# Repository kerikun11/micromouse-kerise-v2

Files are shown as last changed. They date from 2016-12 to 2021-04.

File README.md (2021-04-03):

# MicroMouse KERISE v2

クラッシクサイズおよびハーフサイズ兼用マイクロマウス

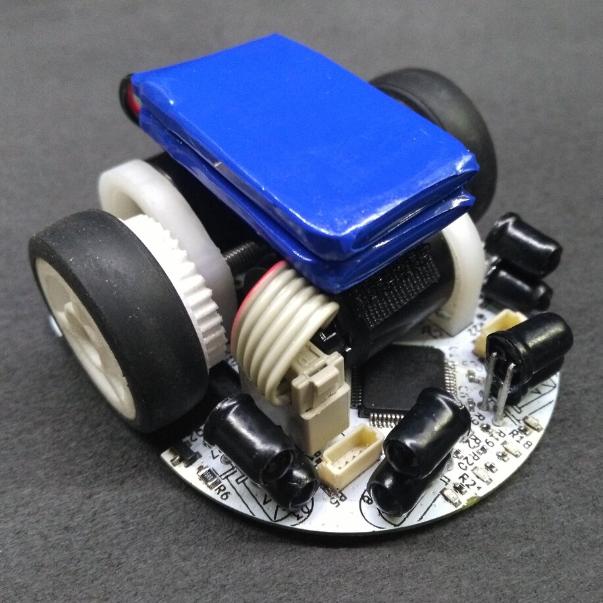
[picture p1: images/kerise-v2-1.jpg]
KERISE v2


## 戦績

なし

## スペック

| 部品 | 型番 | 備考 |
| :--- | :--- | :--- |
| モーター | 1717T006SR | 17mm x 17mm |
| エンコーダ | IEH2-1024 | 1024パルス モーター直結 |
| マイコン | STM32F405RG | 168MHz |
| 赤外線LED | VSLY5850 | 波長850mm 直径5mm |
| フォトダイオード | SFH213FA | 波長900nm 直径5mm |
| モータードライバ | DRV8835 | 最大電流3A |
| 6軸センサ | MPU6500 | 3軸ジャイロ+3軸加速度 |
| バッテリー | LG325-0120-1S-M | 3.7V 25C 120mAh 1S |

## 回路設計

- KiCad

## 開発環境

- mbed RTOS

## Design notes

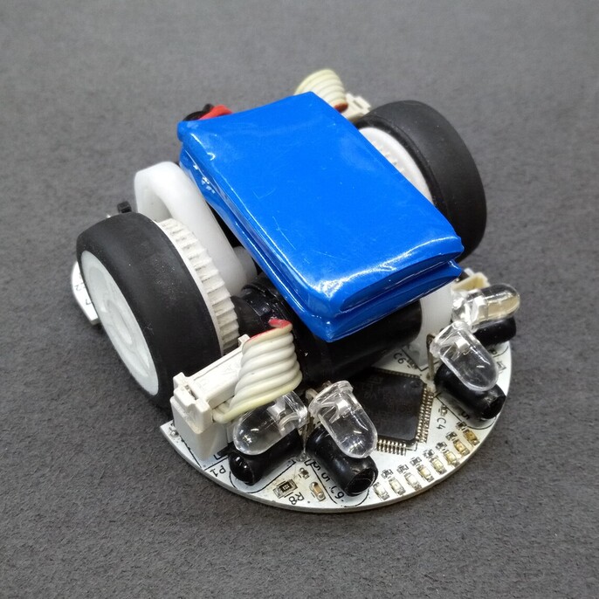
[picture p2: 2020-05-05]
images/kerise-v2-2.jpg

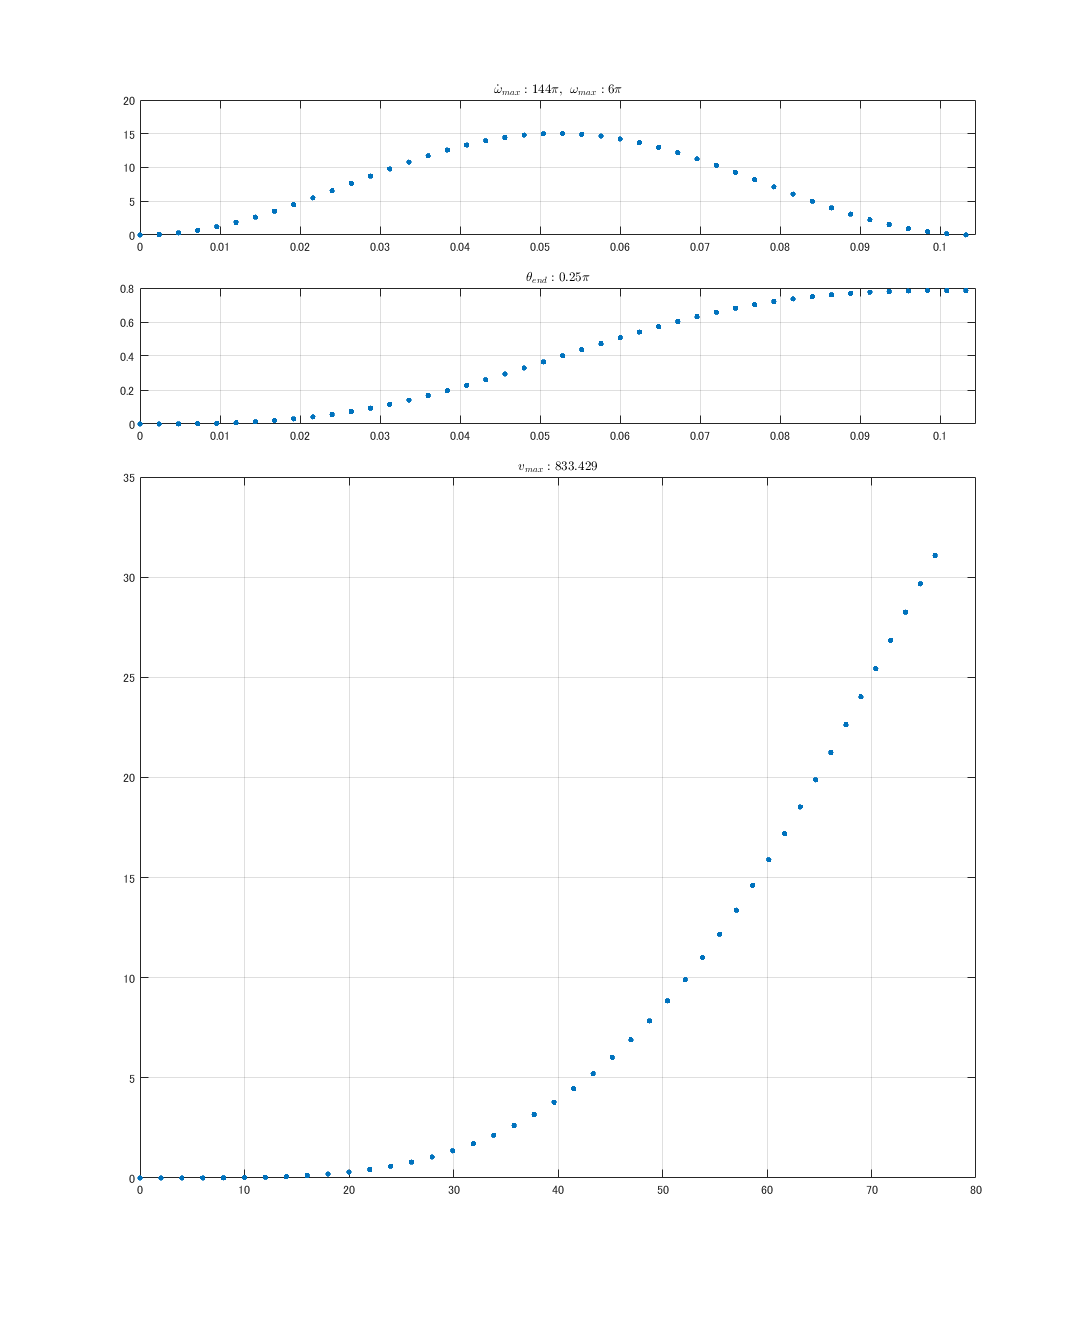
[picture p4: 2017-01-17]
matlab/half45.png

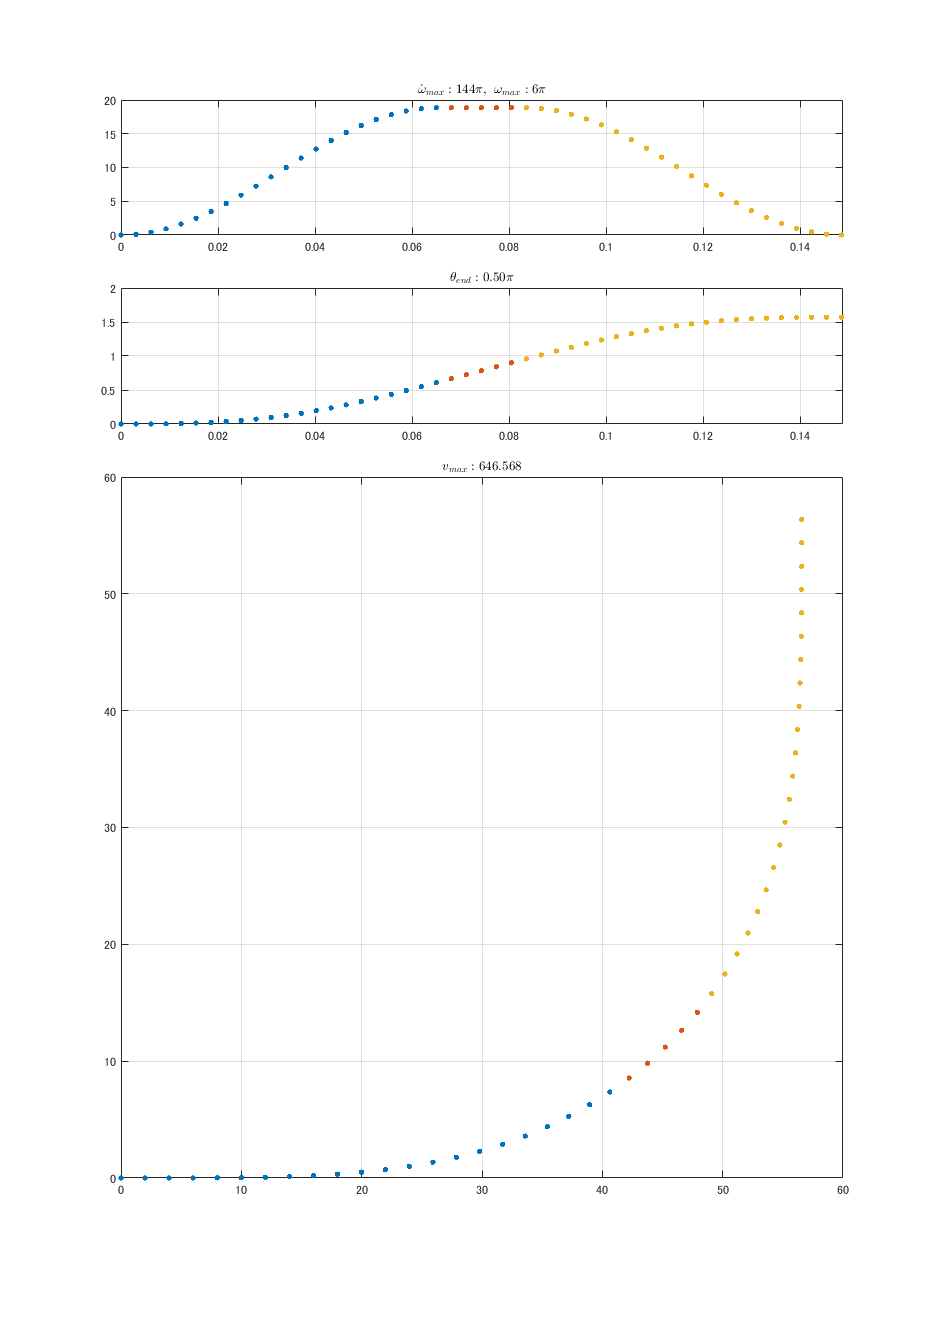
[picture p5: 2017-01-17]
matlab/half4545.png

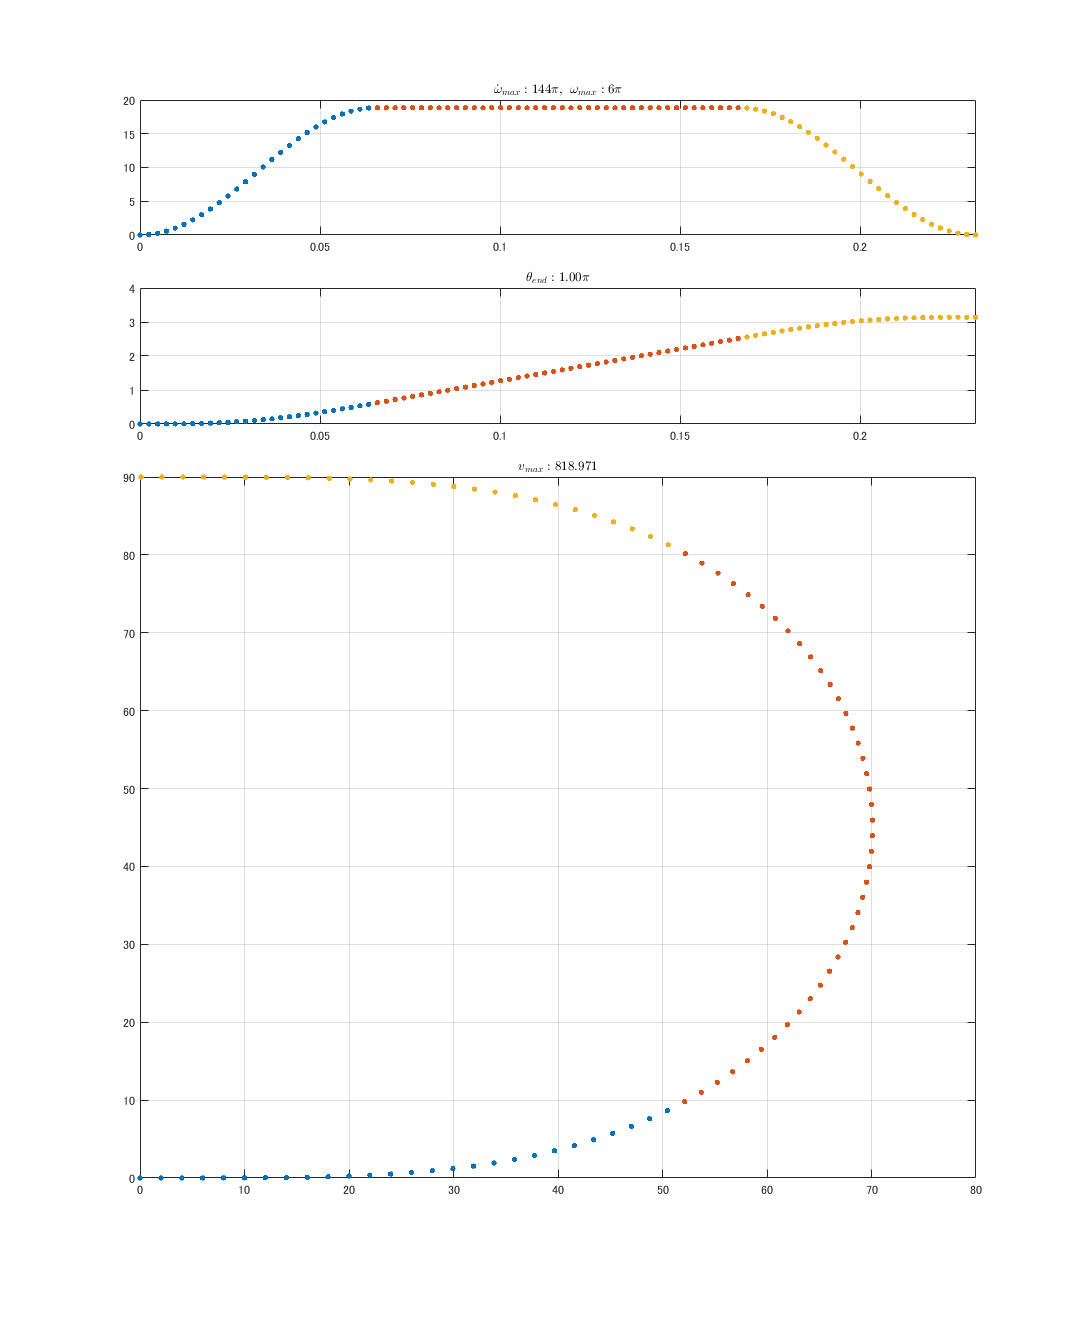
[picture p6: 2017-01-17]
matlab/half180.png

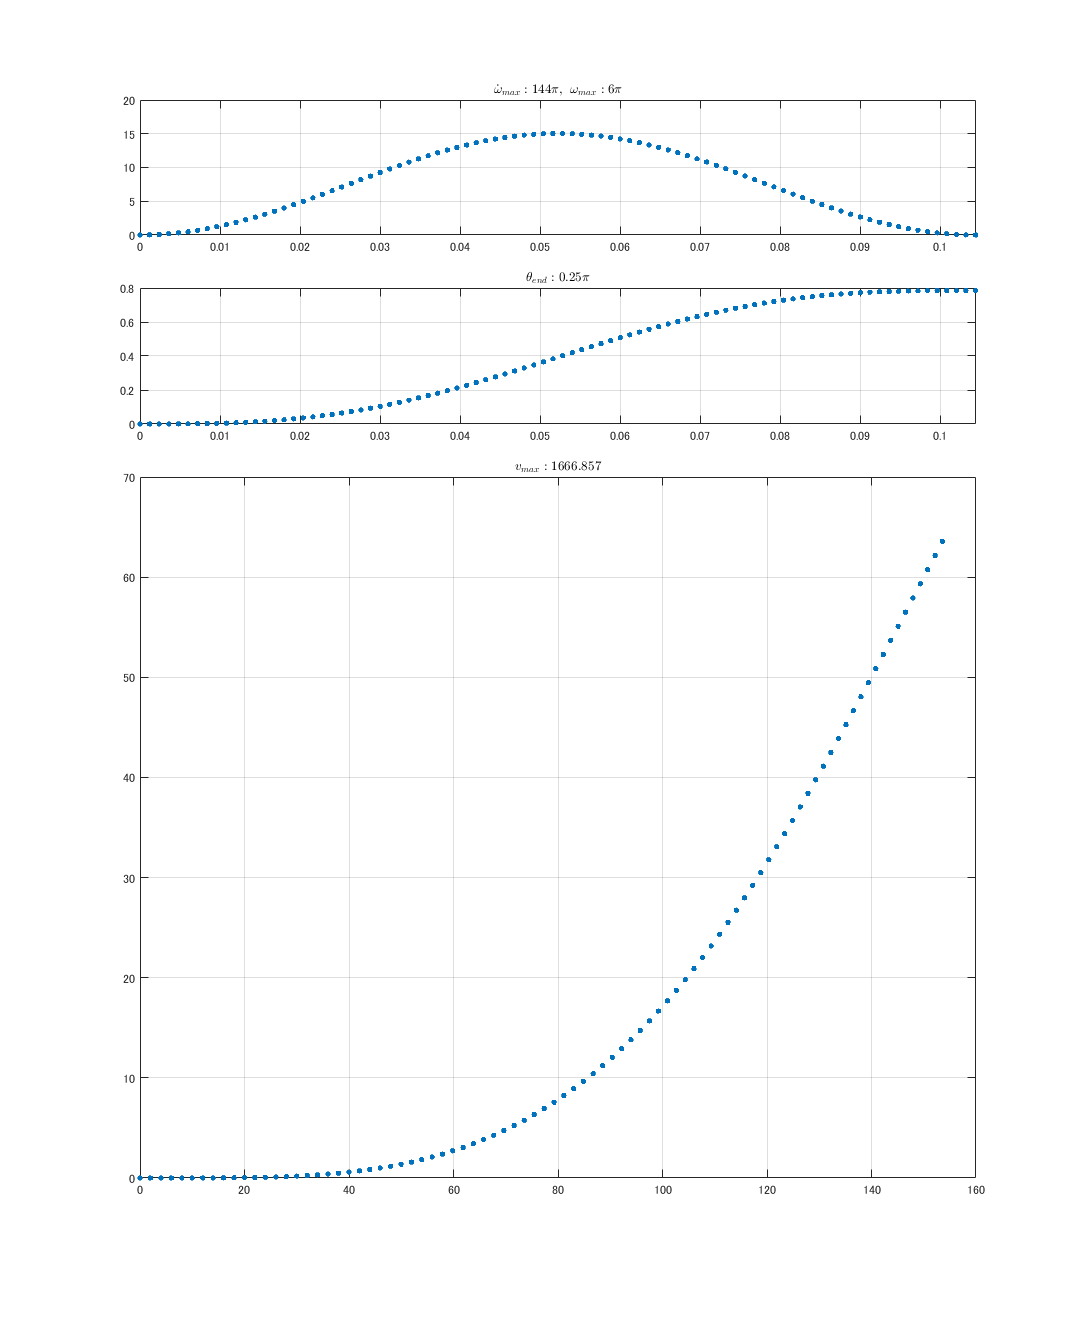
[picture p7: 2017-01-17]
matlab/classic45.png

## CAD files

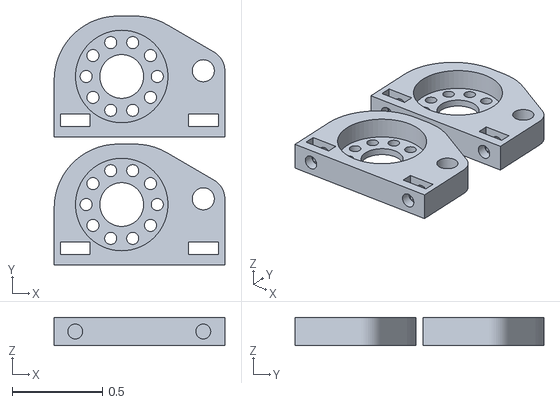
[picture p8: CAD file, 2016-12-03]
3dcad/-4digree.stl
0.945 x 1.38 x 0.157

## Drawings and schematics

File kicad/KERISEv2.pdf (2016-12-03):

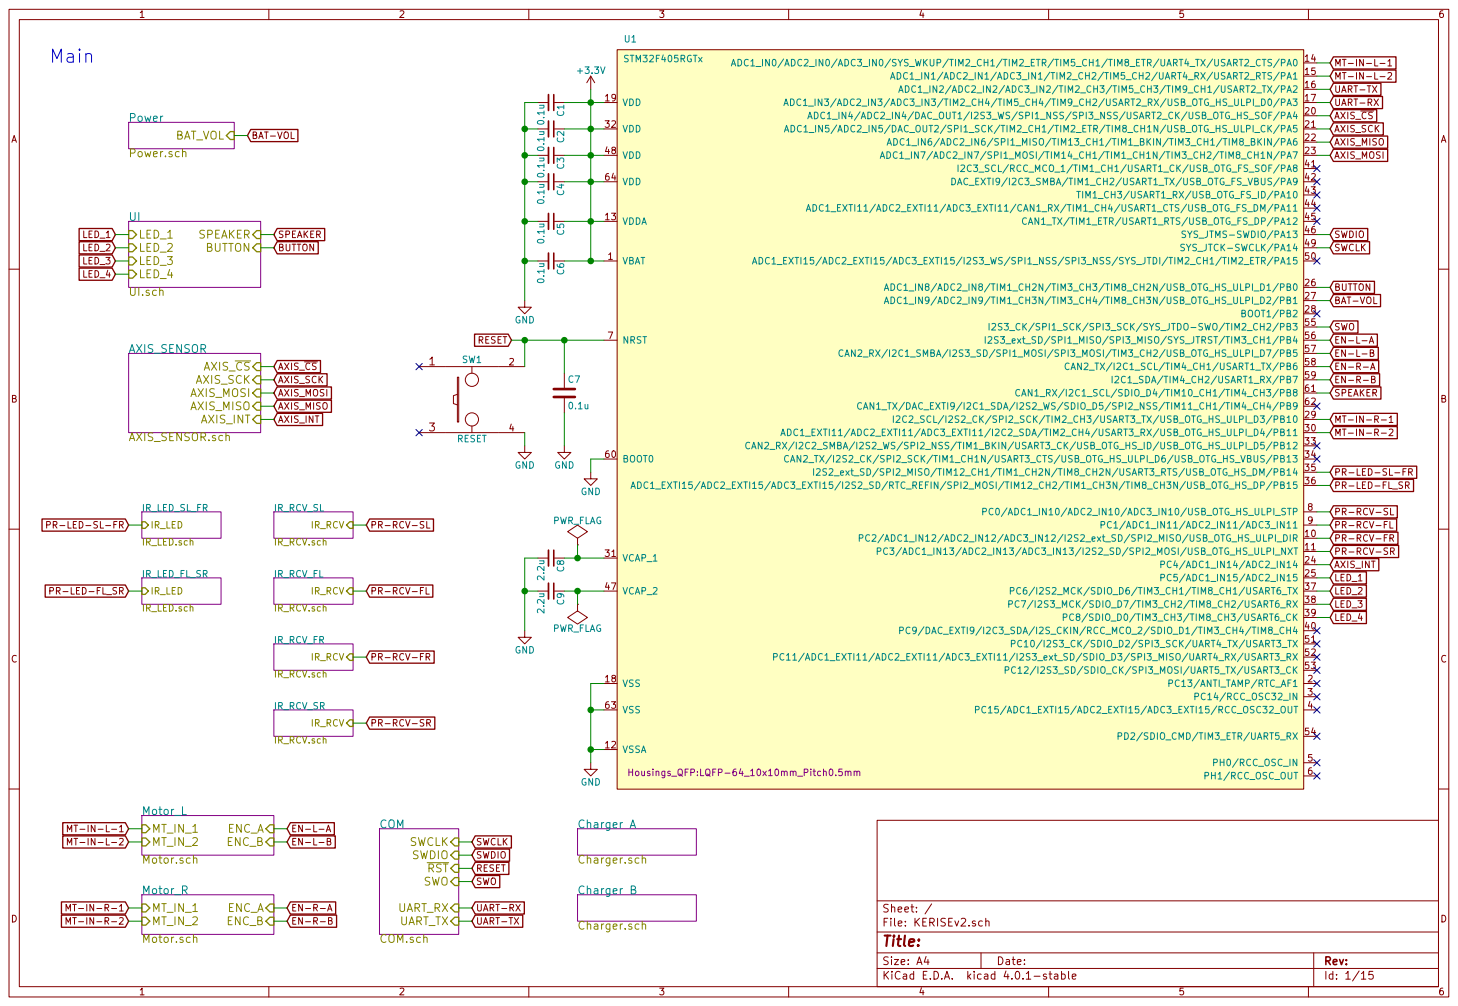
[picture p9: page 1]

UART-RX UART-TX

PR-LED-SL-FR

PR-RCV-SL PR-RCV-FL PR-RCV-FR

Id: 1/15 Title: File: KERISEv2.sch Sheet: /

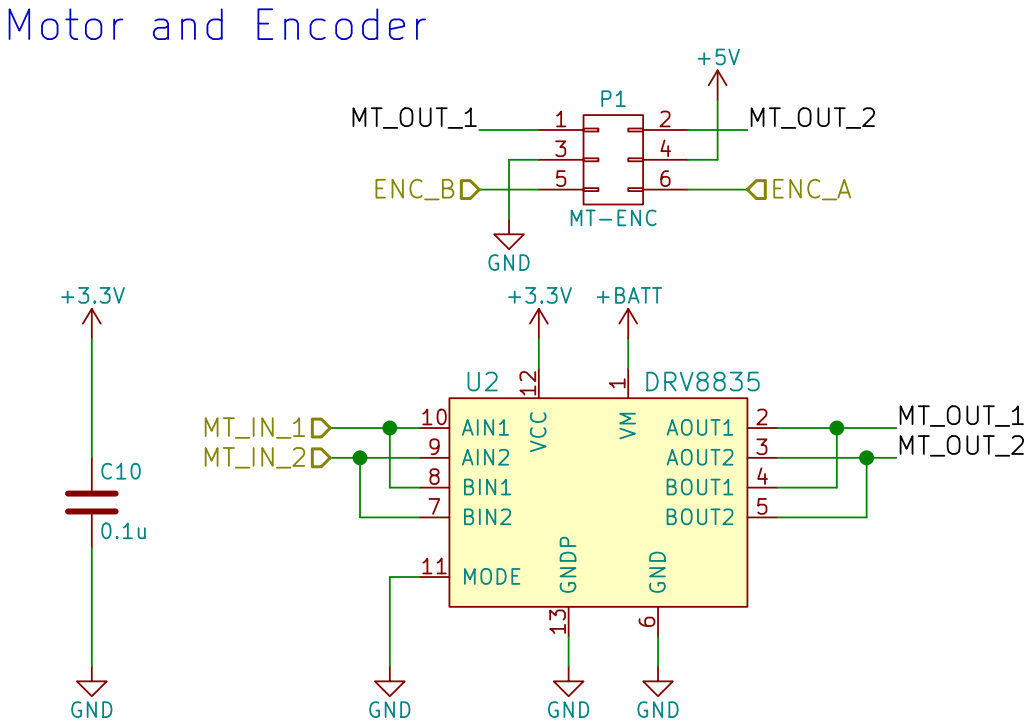
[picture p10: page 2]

1 AOUT1 2 AOUT2 3 BOUT1 4 BOUT2 5 GND
Id: 2/15 Title: File: Motor.sch Sheet: /Motor_L/ VM

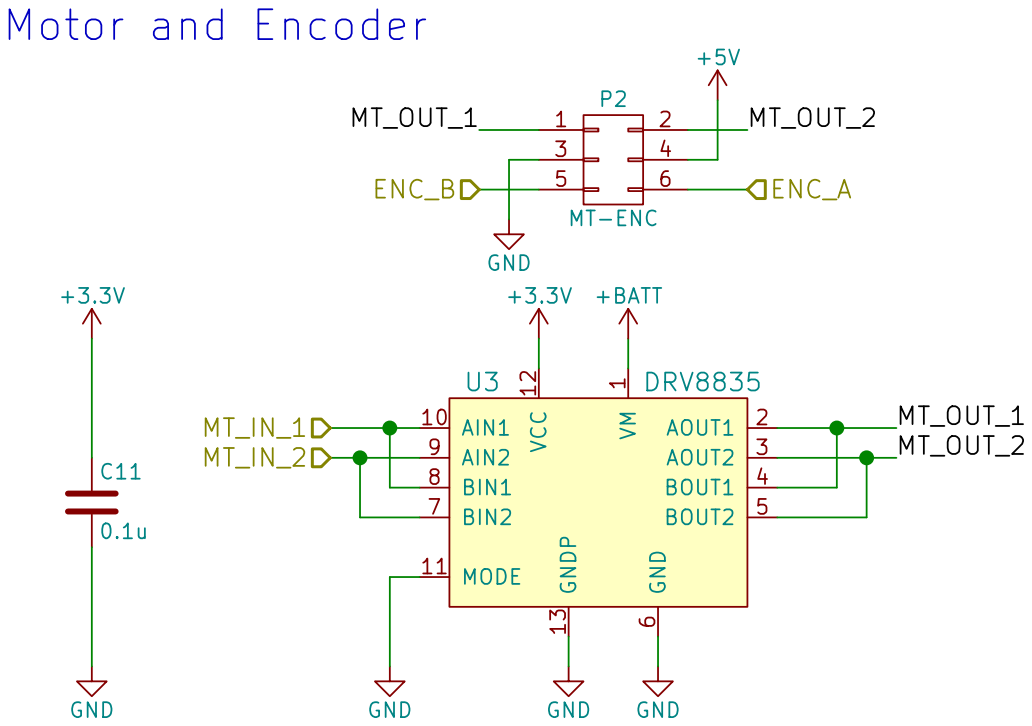
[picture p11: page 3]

1 AOUT1 2 AOUT2 3 BOUT1 4 BOUT2 5 GND
Id: 3/15 Title: File: Motor.sch Sheet: /Motor_R/ VM

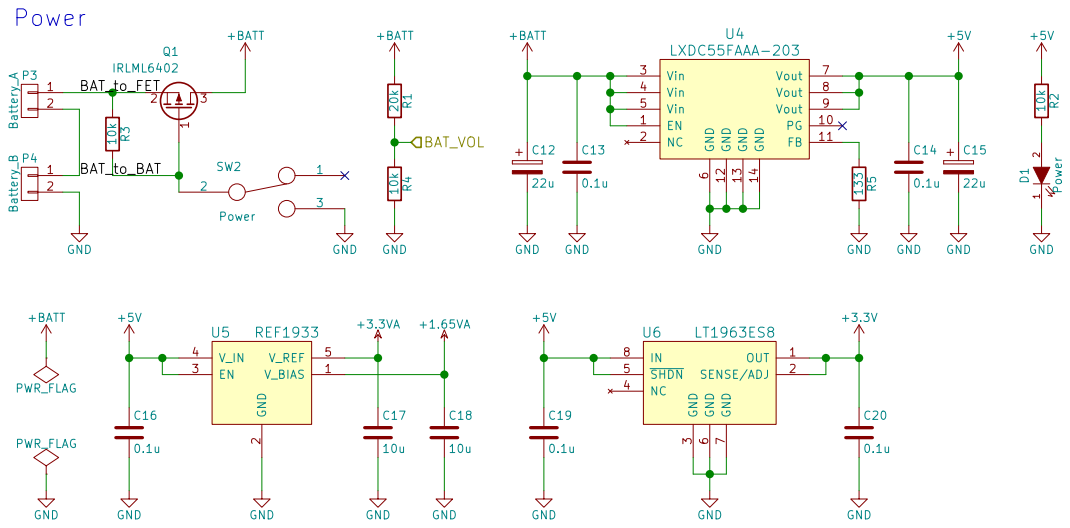
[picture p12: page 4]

6 Vout 7 Vout 8 Vout 9 PG 10 FB 11 GND 12 GND 13 GND 14 U4

Id: 4/15 Title: File: Power.sch Sheet: /Power/

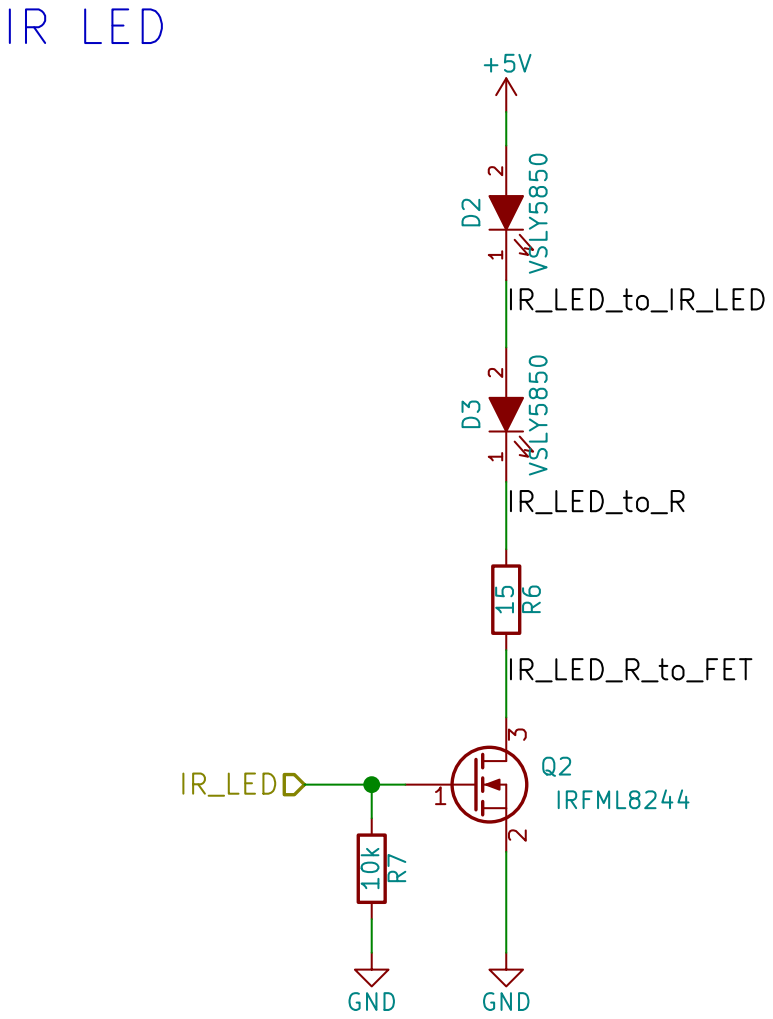
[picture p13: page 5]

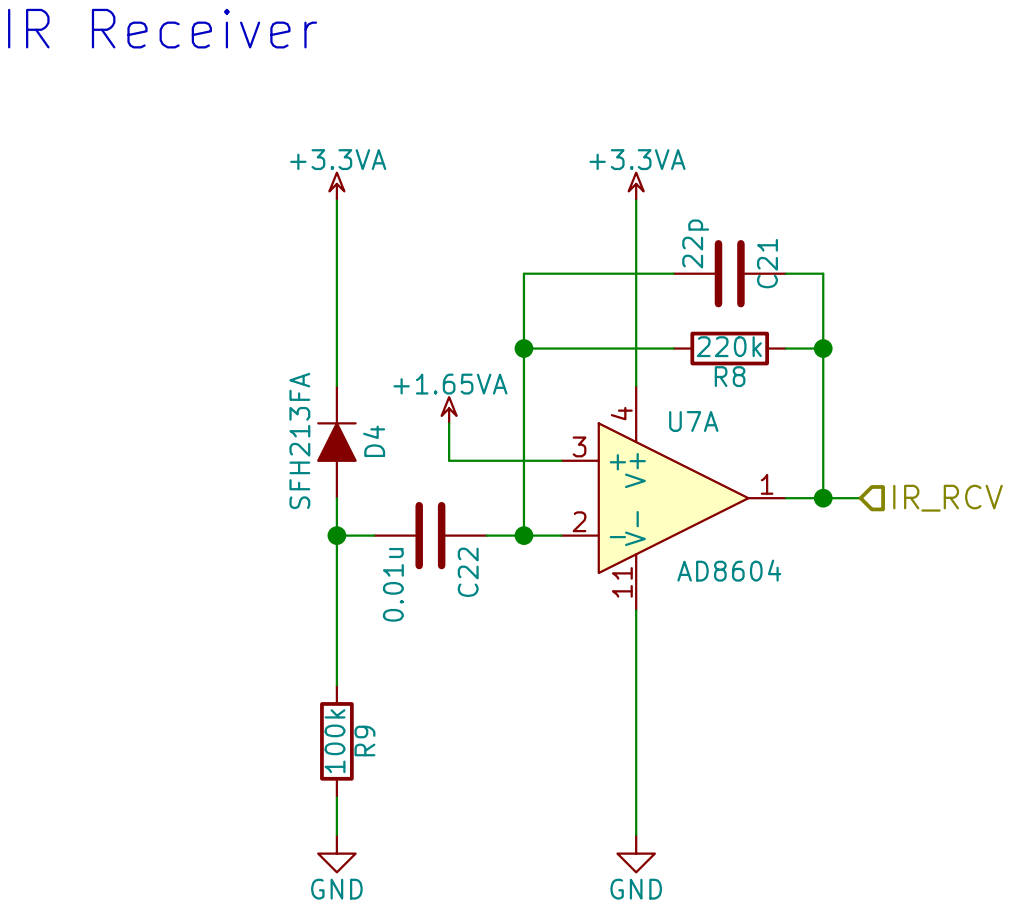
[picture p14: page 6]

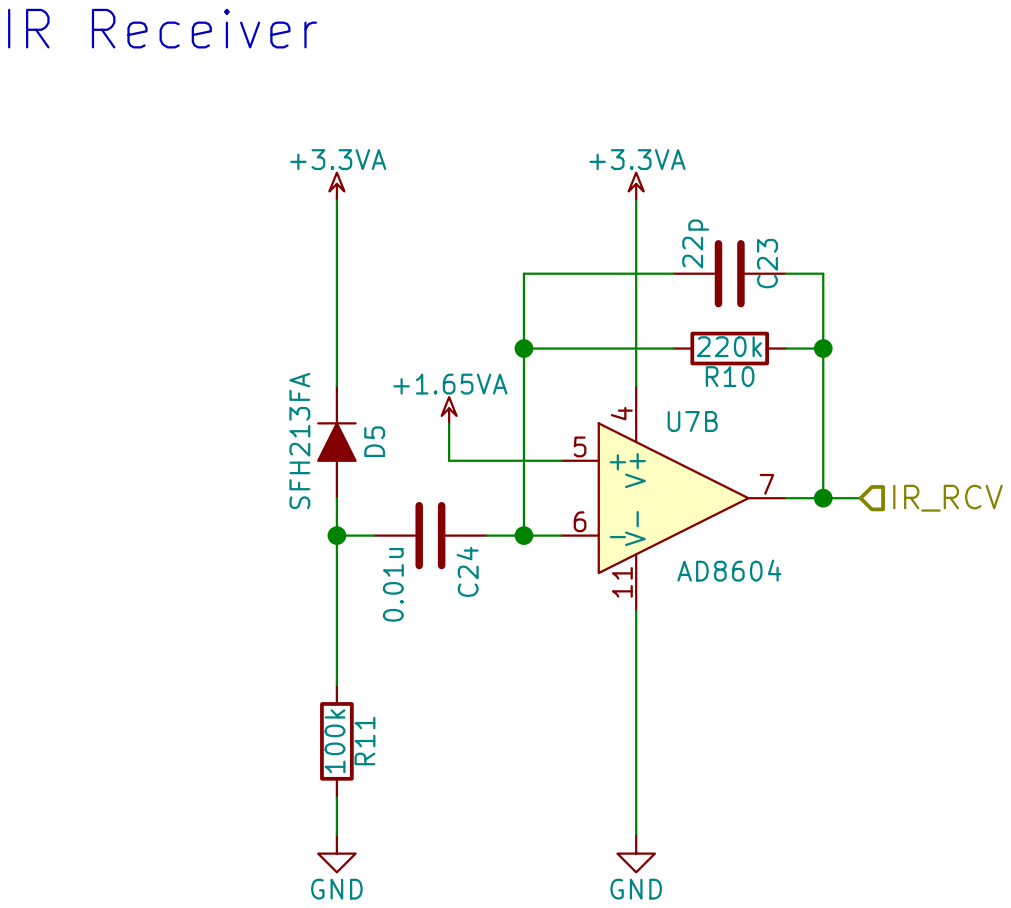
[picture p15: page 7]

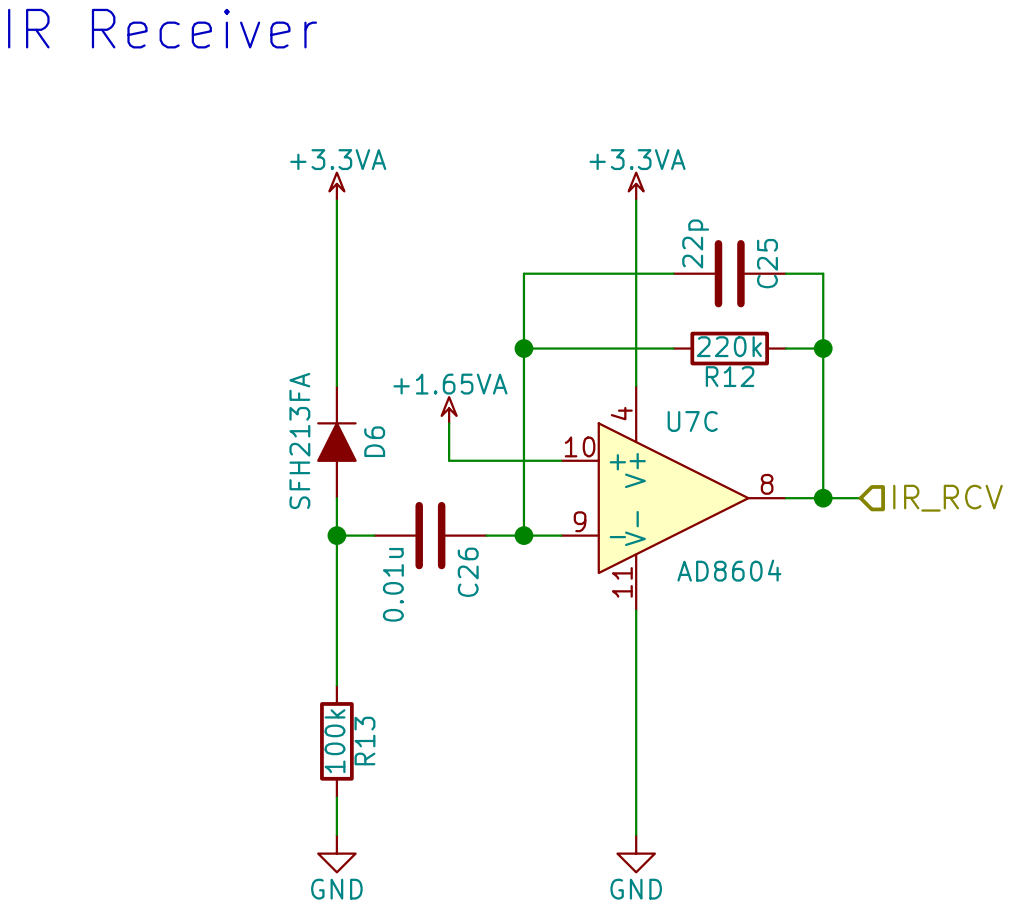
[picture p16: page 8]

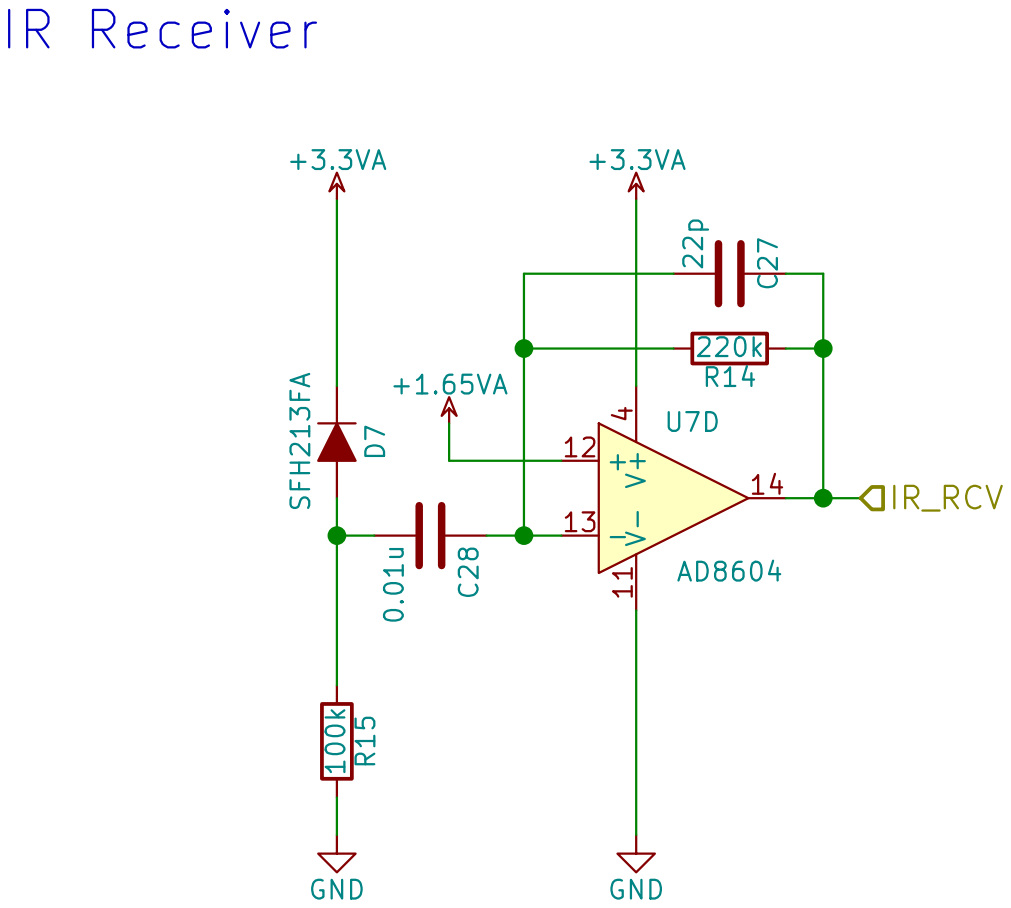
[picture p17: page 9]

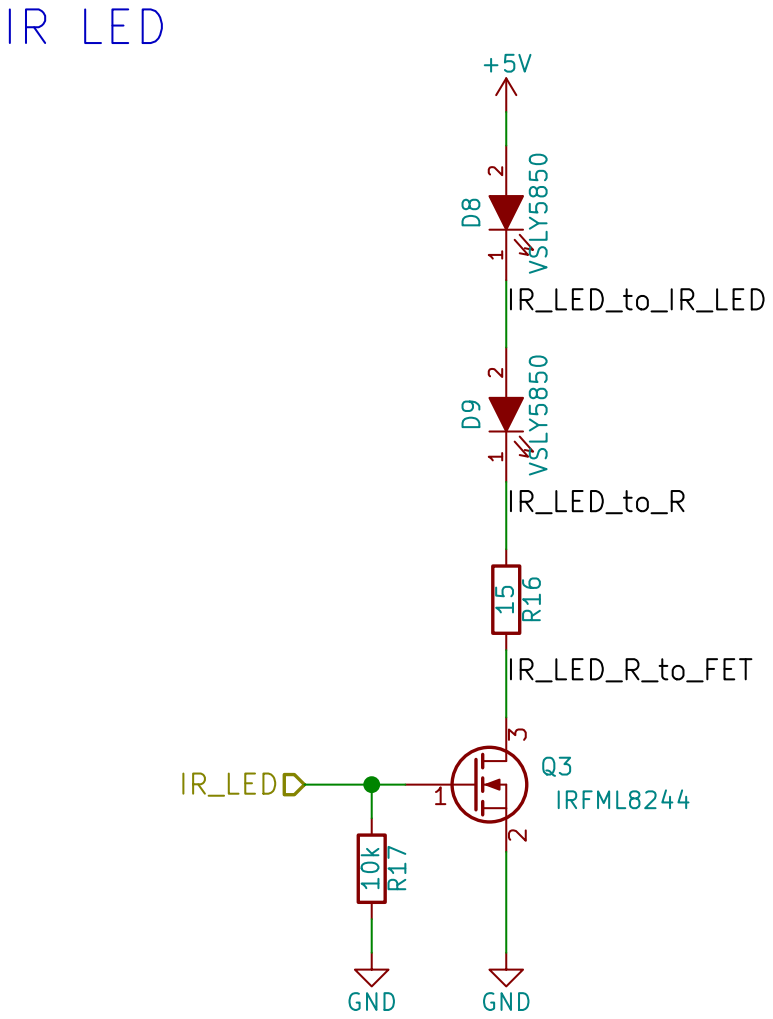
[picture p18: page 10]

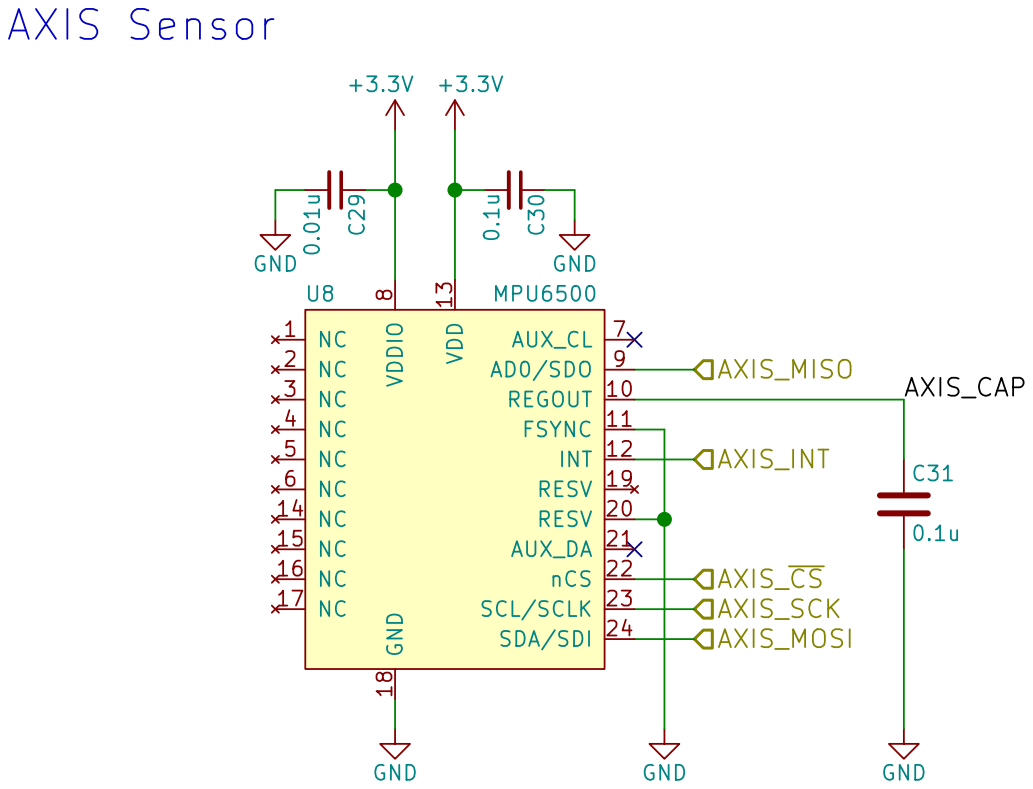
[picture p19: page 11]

8 AD0/SDO 9 REGOUT 10 RESV 20 FSYNC 11 AUX_DA 21

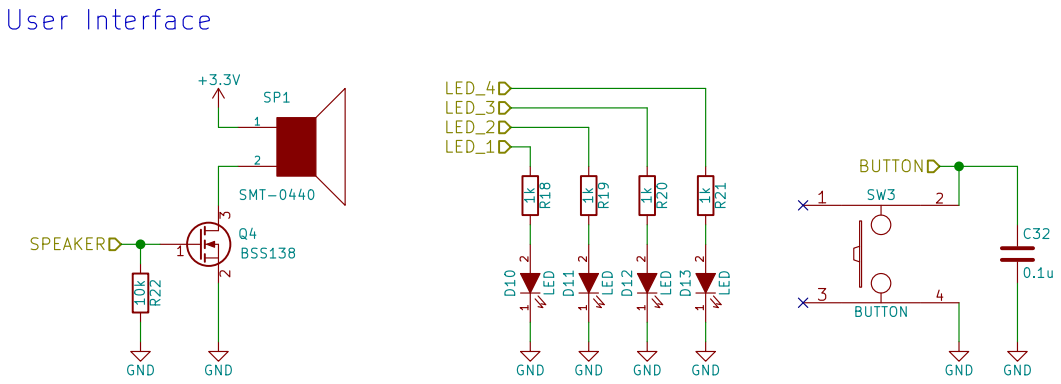
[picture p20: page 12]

1 2 D13 LED GND GND GND GND R18 1k R19 1k R20 1k R21 1k

Id: 12/15 Title: File: UI.sch Sheet: /UI/


Id: 13/15 Title: File: COM.sch Sheet: /COM/ SWCLK


2 VBAT 3 VDD 4 PROG 5 U10 MCP73831 4.7k R25 STAT 1 VSS


2 VBAT 3 VDD 4 PROG 5 U12 MCP73831 4.7k R29 STAT 1 VSS

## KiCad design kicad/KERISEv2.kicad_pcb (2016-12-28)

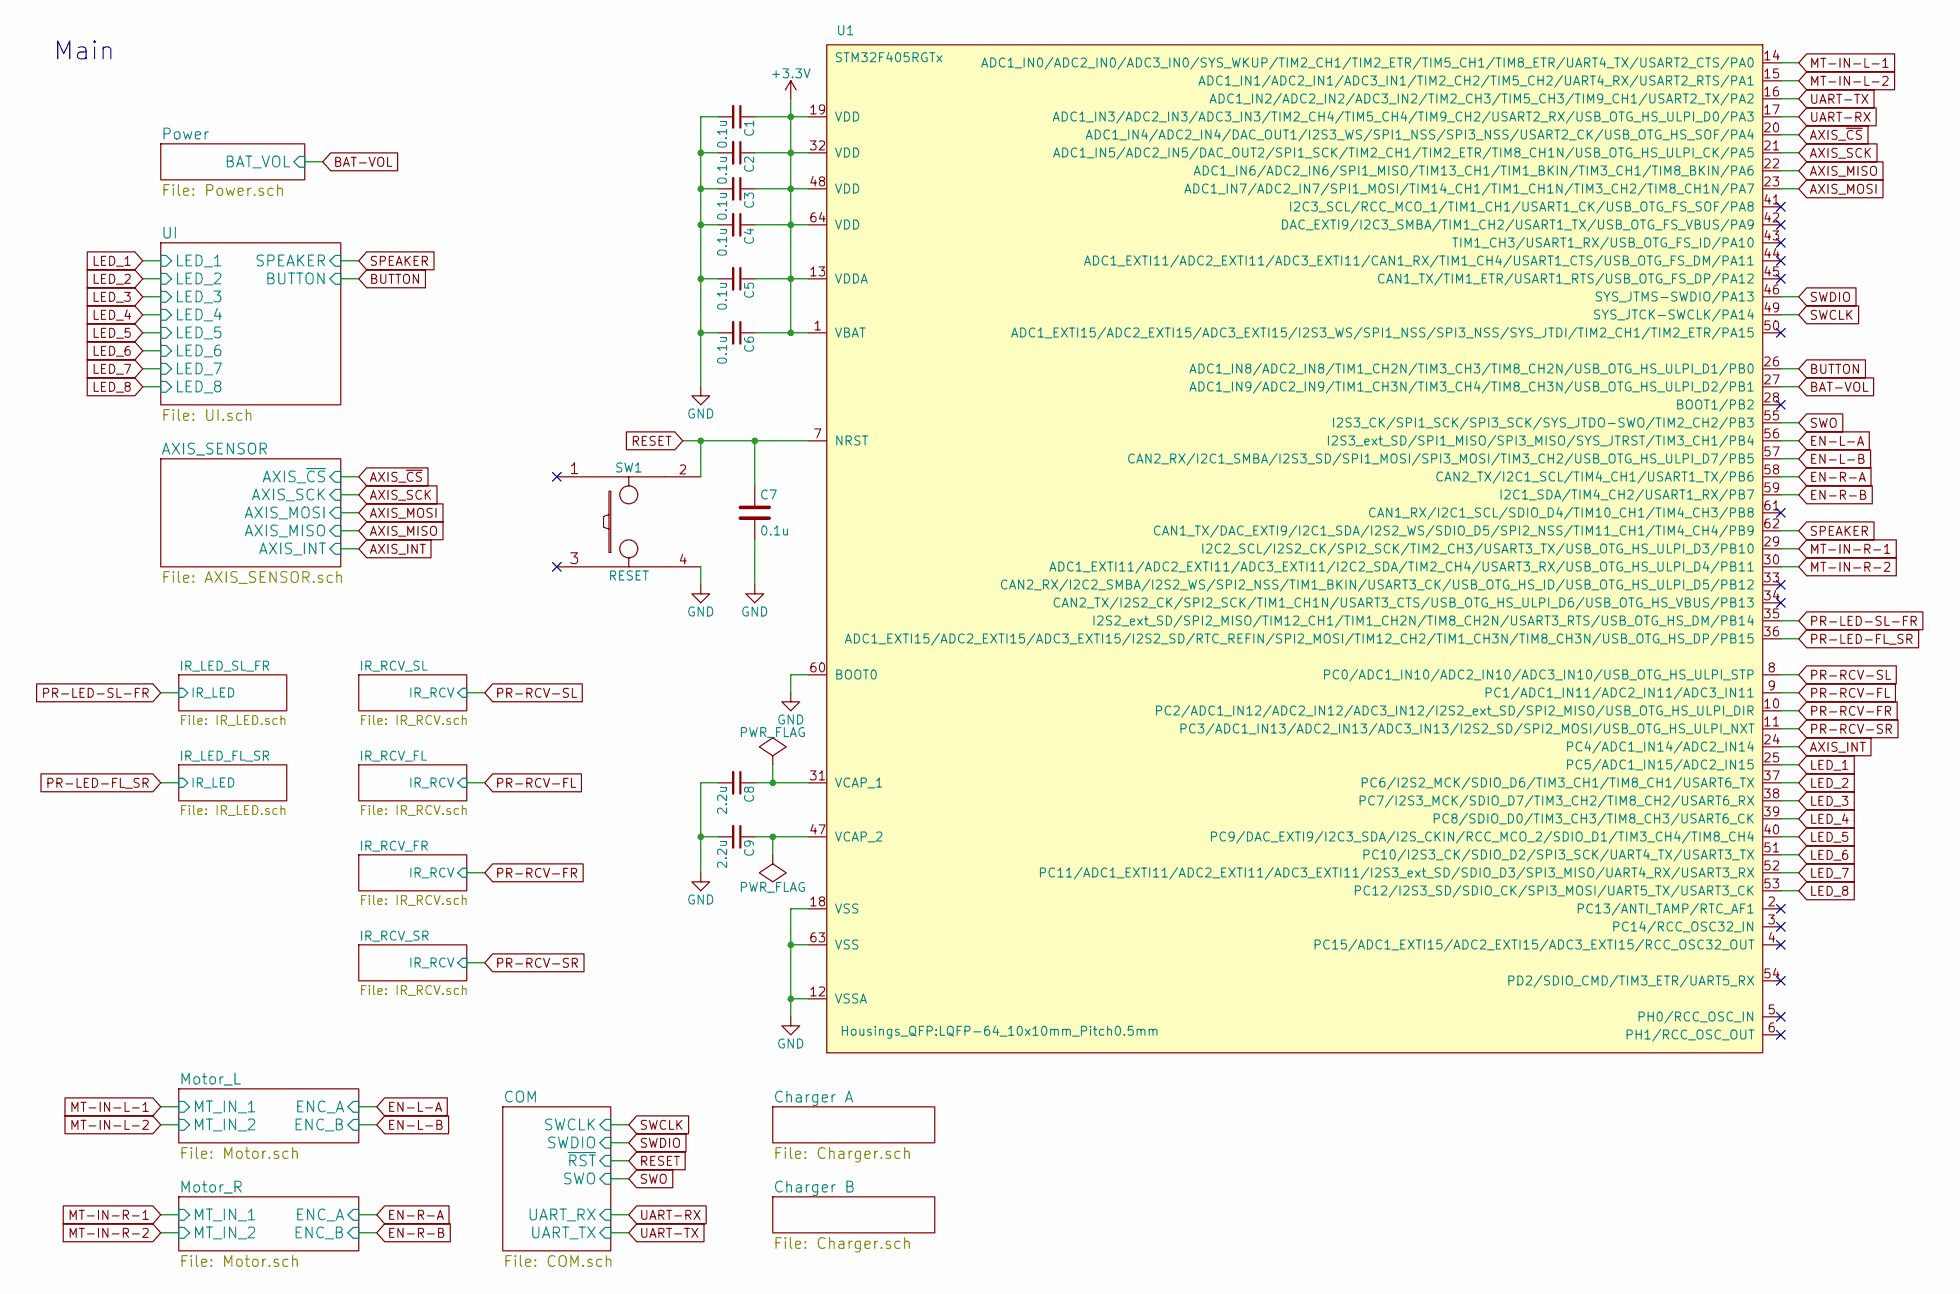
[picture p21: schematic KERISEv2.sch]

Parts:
C1, C2, C3, C4, C5, C6, C7: 0.1u; C_0402
C8, C9: 2.2u; C_0603
SW1: RESET; SW_PUSH
U1: STM32F405RGTx; LQFP-64_10x10mm_Pitch0.5mm

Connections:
+3V3: C1.1, C2.1, C3.1, C4.1, C5.1, C6.1, U1.1 (VBAT), U1.13 (VDDA), U1.19 (VDD), U1.32 (VDD), U1.48 (VDD), U1.64 (VDD); also elsewhere on the board
AXIS_INT: U1.24 (PC4/ADC1_IN14/ADC2_IN14); also elsewhere on the board
AXIS_MISO: U1.22 (ADC1_IN6/ADC2_IN6/SPI1_MISO/TIM13_CH1/T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); also elsewhere on the board
AXIS_MOSI: U1.23 (ADC1_IN7/ADC2_IN7/SPI1_MOSI/TIM14_CH1/T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); also elsewhere on the board
AXIS_SCK: U1.21 (ADC1_IN5/ADC2_IN5/DAC_OUT2/SPI1_SCK/TIM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); also elsewhere on the board
AXIS_~CS: U1.20 (ADC1_IN4/ADC2_IN4/DAC_OUT1/I2S3_WS/SPI1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); also elsewhere on the board
BAT-VOL: U1.27 (ADC1_IN9/ADC2_IN9/TIM1_CH3N/TIM3_CH4/TI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); also elsewhere on the board
BUTTON: U1.26 (ADC1_IN8/ADC2_IN8/TIM1_CH2N/TIM3_CH3/TI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); also elsewhere on the board
EN-L-A: U1.56 (I2S3_ext_SD/SPI1_MISO/SPI3_MISO/SYS_JTR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); also elsewhere on the board
EN-L-B: U1.57 (CAN2_RX/I2C1_SMBA/I2S3_SD/SPI1_MOSI/SPI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); also elsewhere on the board
EN-R-A: U1.58 (CAN2_TX/I2C1_SCL/TIM4_CH1/USART1_TX/PB6); also elsewhere on the board
EN-R-B: U1.59 (I2C1_SDA/TIM4_CH2/USART1_RX/PB7); also elsewhere on the board
GND: C1.2, C2.2, C3.2, C4.2, C5.2, C6.2, C7.2, C8.2, C9.2, SW1.4, U1.12 (VSSA), U1.18 (VSS), U1.60 (BOOT0), U1.63 (VSS); also elsewhere on the board
LED_1: U1.25 (PC5/ADC1_IN15/ADC2_IN15); also elsewhere on the board
LED_2: U1.37 (PC6/I2S2_MCK/SDIO_D6/TIM3_CH1/TIM8_CH1/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); also elsewhere on the board
LED_3: U1.38 (PC7/I2S3_MCK/SDIO_D7/TIM3_CH2/TIM8_CH2/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); also elsewhere on the board
LED_4: U1.39 (PC8/SDIO_D0/TIM3_CH3/TIM8_CH3/USART6_CK); also elsewhere on the board
LED_5: U1.40 (PC9/DAC_EXTI9/I2C3_SDA/I2S_CKIN/RCC_MCO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); also elsewhere on the board
LED_6: U1.51 (PC10/I2S3_CK/SDIO_D2/SPI3_SCK/UART4_TX/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); also elsewhere on the board
LED_7: U1.52 (PC11/ADC1_EXTI11/ADC2_EXTI11/ADC3_EXTI1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); also elsewhere on the board
LED_8: U1.53 (PC12/I2S3_SD/SDIO_CK/SPI3_MOSI/UART5_TX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); also elsewhere on the board
MT-IN-L-1: U1.14 (ADC1_IN0/ADC2_IN0/ADC3_IN0/SYS_WKUP/TIM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); also elsewhere on the board
MT-IN-L-2: U1.15 (ADC1_IN1/ADC2_IN1/ADC3_IN1/TIM2_CH2/TIM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); also elsewhere on the board
MT-IN-R-1: U1.29 (I2C2_SCL/I2S2_CK/SPI2_SCK/TIM2_CH3/USAR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); also elsewhere on the board
MT-IN-R-2: U1.30 (ADC1_EXTI11/ADC2_EXTI11/ADC3_EXTI11/I2C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); also elsewhere on the board
unnamed: C8.1, U1.31 (VCAP_1)
unnamed: C9.1, U1.47 (VCAP_2)
PR-LED-FL_SR: U1.36 (ADC1_EXTI15/ADC2_EXTI15/ADC3_EXTI15/I2S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); also elsewhere on the board
PR-LED-SL-FR: U1.35 (I2S2_ext_SD/SPI2_MISO/TIM12_CH1/TIM1_CH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); also elsewhere on the board
PR-RCV-FL: U1.9 (PC1/ADC1_IN11/ADC2_IN11/ADC3_IN11); also elsewhere on the board
PR-RCV-SR: U1.11 (PC3/ADC1_IN13/ADC2_IN13/ADC3_IN13/I2S2_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); also elsewhere on the board
RESET: C7.1, SW1.2, U1.7 (NRST); also elsewhere on the board
SPEAKER: U1.62 (CAN1_TX/DAC_EXTI9/I2C1_SDA/I2S2_WS/SDIO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); also elsewhere on the board
SWCLK: U1.49 (SYS_JTCK-SWCLK/PA14); also elsewhere on the board
SWDIO: U1.46 (SYS_JTMS-SWDIO/PA13); also elsewhere on the board
SWO: U1.55 (I2S3_CK/SPI1_SCK/SPI3_SCK/SYS_JTDO-SWO/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); also elsewhere on the board
UART-RX: U1.17 (ADC1_IN3/ADC2_IN3/ADC3_IN3/TIM2_CH4/TIM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); also elsewhere on the board
UART-TX: U1.16 (ADC1_IN2/ADC2_IN2/ADC3_IN2/TIM2_CH3/TIM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); also elsewhere on the board

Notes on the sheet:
Main

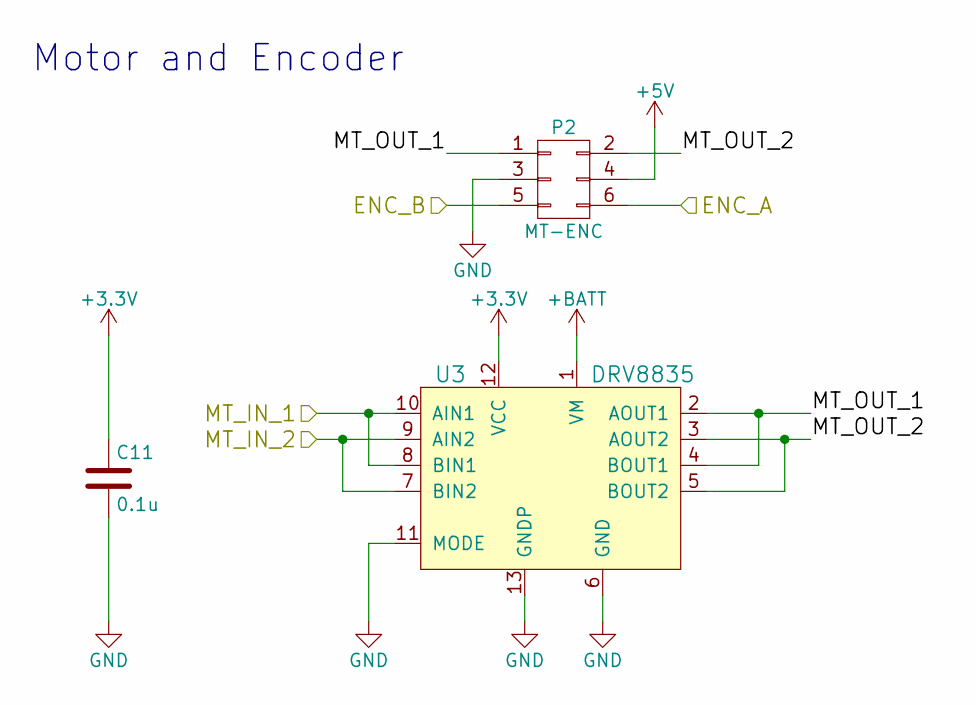
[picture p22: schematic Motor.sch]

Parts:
C10: 0.1u; C_0402
P1: MT-ENC; 1717
U2: DRV8835

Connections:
+3V3: C10.1, U2.12 (VCC); also elsewhere on the board
+5V: P1.4; also elsewhere on the board
+BATT: U2.1 (VM); also elsewhere on the board
/Motor_L/MT_OUT_1: P1.1, U2.2 (AOUT1), U2.4 (BOUT1)
/Motor_L/MT_OUT_2: P1.2, U2.3 (AOUT2), U2.5 (BOUT2)
EN-L-A: P1.6; also elsewhere on the board
EN-L-B: P1.5; also elsewhere on the board
GND: C10.2, P1.3, U2.6 (GND), U2.11 (MODE), U2.13 (GNDP); also elsewhere on the board
MT-IN-L-1: U2.8 (BIN1), U2.10 (AIN1); also elsewhere on the board
MT-IN-L-2: U2.7 (BIN2), U2.9 (AIN2); also elsewhere on the board

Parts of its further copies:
C11: 0.1u; C_0402
P2: MT-ENC; 1717
U3: DRV8835

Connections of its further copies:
+3V3: C11.1, U3.12 (VCC); also elsewhere on the board
+5V: P2.4; also elsewhere on the board
+BATT: U3.1 (VM); also elsewhere on the board
/Motor_R/MT_OUT_1: P2.1, U3.2 (AOUT1), U3.4 (BOUT1)
/Motor_R/MT_OUT_2: P2.2, U3.3 (AOUT2), U3.5 (BOUT2)
EN-R-A: P2.6; also elsewhere on the board
EN-R-B: P2.5; also elsewhere on the board
GND: C11.2, P2.3, U3.6 (GND), U3.11 (MODE), U3.13 (GNDP); also elsewhere on the board
MT-IN-R-1: U3.8 (BIN1), U3.10 (AIN1); also elsewhere on the board
MT-IN-R-2: U3.7 (BIN2), U3.9 (AIN2); also elsewhere on the board

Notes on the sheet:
Motor and Encoder

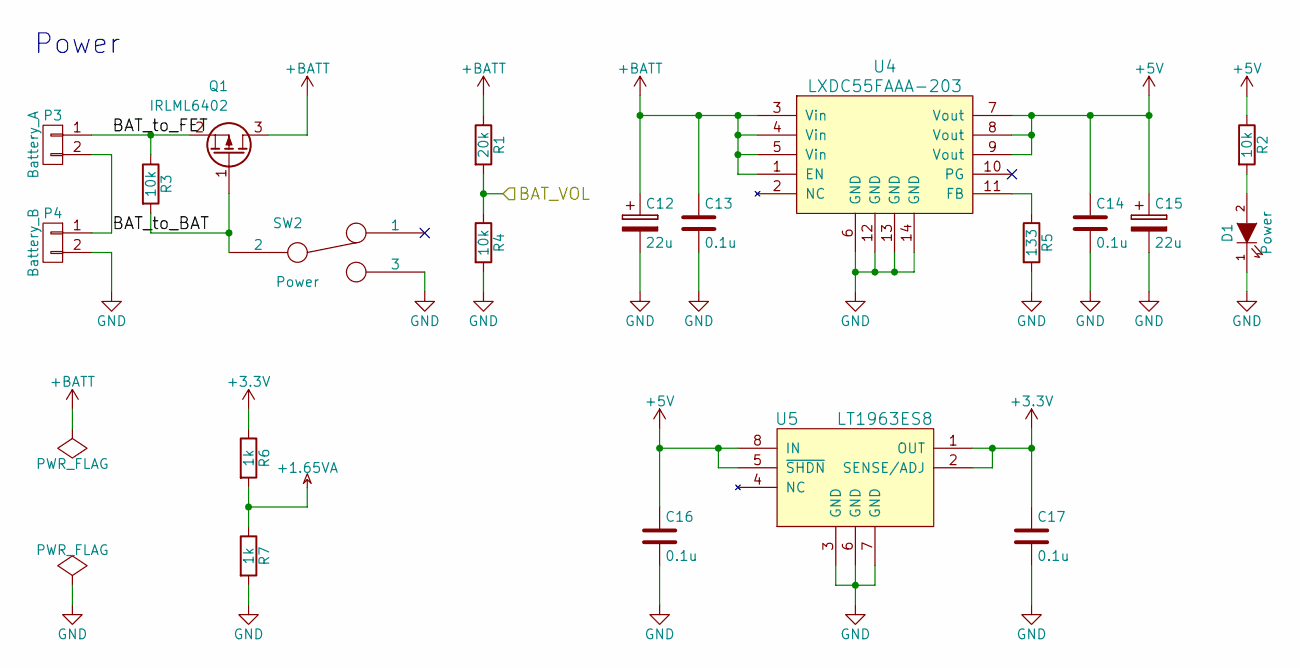
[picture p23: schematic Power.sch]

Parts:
C12, C15: 22u; C_0805
C13, C14, C16, C17: 0.1u; C_0402
D1: Power; LED_0603
P3: Battery_A; Hirose_DF13-02P-1.25DSA_02x1.25mm_Straight
P4: Battery_B; Hirose_DF13-02P-1.25DSA_02x1.25mm_Straight
Q1: IRLML6402; SOT-23
R1: 20k; R_0402
R2, R3, R4: 10k; R_0402
R5: 133; R_0402
R6, R7: 1k; R_0402
SW2: Power; Slide_SW
U4: LXDC55FAAA-203
U5: LT1963ES8; SOIC-8_3.9x4.9mm_Pitch1.27mm

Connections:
+1.65VA: R6.2, R7.1; also elsewhere on the board
+3V3: C17.1, R6.1, U5.1 (OUT), U5.2 (SENSE/ADJ); also elsewhere on the board
+5V: C14.1, C15.1, C16.1, R2.1, U4.7 (Vout), U4.8 (Vout), U4.9 (Vout), U5.5 (~SHDN), U5.8 (IN); also elsewhere on the board
+BATT: C12.1, C13.1, Q1.3 (D), R1.1, U4.1 (EN), U4.3 (Vin), U4.4 (Vin), U4.5 (Vin); also elsewhere on the board
/Power/BAT_to_BAT: P3.2, P4.1
/Power/BAT_to_FET: P3.1, Q1.2 (S), R3.1
BAT-VOL: R1.2, R4.1; also elsewhere on the board
GND: C12.2, C13.2, C14.2, C15.2, C16.2, C17.2, D1.1 (K), P4.2, R4.2, R5.2, R7.2, SW2.3, U4.6 (GND), U4.12 (GND), U4.13 (GND), U4.14 (GND), U5.3 (GND), U5.6 (GND), U5.7 (GND); also elsewhere on the board
unnamed: D1.2 (A), R2.2
unnamed: Q1.1 (G), R3.2, SW2.2
unnamed: R5.1, U4.11 (FB)

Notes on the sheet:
Power

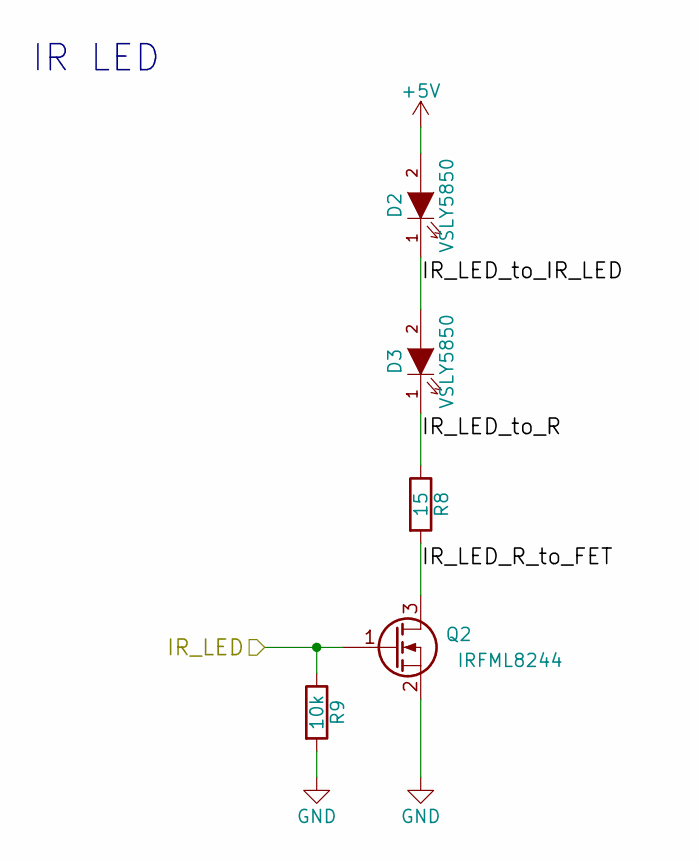
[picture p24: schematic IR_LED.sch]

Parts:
D2: VSLY5850; LED-5MM_Angle_wide
D3: VSLY5850; LED-5MM_Angle
Q2: IRFML8244; SOT-23
R8: 15; R_0805
R9: 10k; R_0402

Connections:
+5V: D2.2 (A); also elsewhere on the board
/IR_LED_SL_FR/IR_LED_R_to_FET: Q2.3 (D), R8.2
/IR_LED_SL_FR/IR_LED_to_IR_LED: D2.1 (K), D3.2 (A)
/IR_LED_SL_FR/IR_LED_to_R: D3.1 (K), R8.1
GND: Q2.2 (S), R9.2; also elsewhere on the board
PR-LED-SL-FR: Q2.1 (G), R9.1; also elsewhere on the board

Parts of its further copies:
D8: VSLY5850; LED-5MM_Angle_wide
D9: VSLY5850; LED-5MM_Angle
Q3: IRFML8244; SOT-23
R18: 15; R_0805
R19: 10k; R_0402

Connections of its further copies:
+5V: D8.2 (A); also elsewhere on the board
/IR_LED_FL_SR/IR_LED_R_to_FET: Q3.3 (D), R18.2
/IR_LED_FL_SR/IR_LED_to_IR_LED: D8.1 (K), D9.2 (A)
/IR_LED_FL_SR/IR_LED_to_R: D9.1 (K), R18.1
GND: Q3.2 (S), R19.2; also elsewhere on the board
PR-LED-FL_SR: Q3.1 (G), R19.1; also elsewhere on the board

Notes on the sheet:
IR LED

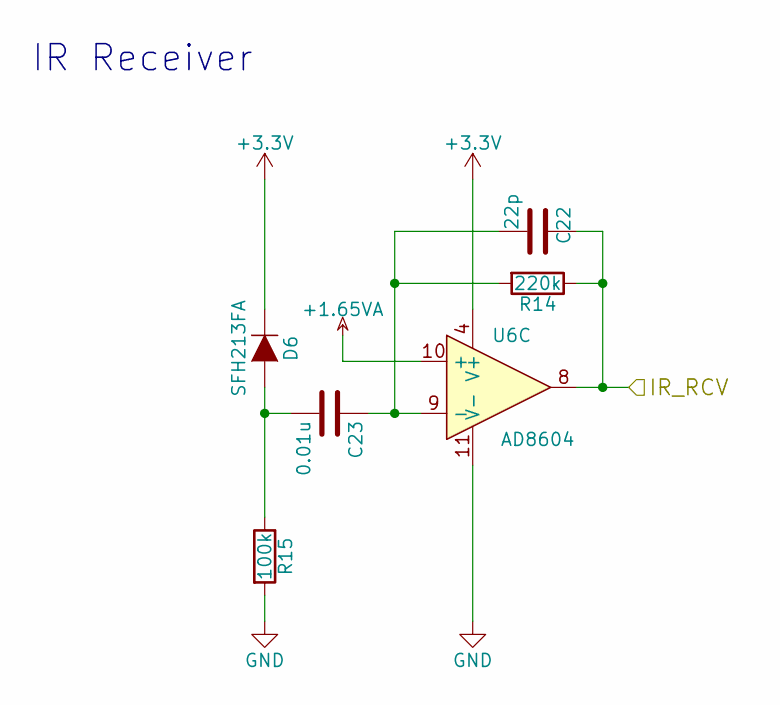
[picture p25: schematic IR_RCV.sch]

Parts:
C18: 22p; C_0402
C19: 0.01u; C_0402
D4: SFH213FA; Photo-5MM_Angle
R10: 220k; R_0402
R11: 100k; R_0402
U6: AD8604; TSSOP-14_4.4x5mm_Pitch0.65mm

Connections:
+1.65VA: U6.3 (+), U6.5 (+), U6.10 (+), U6.12 (+); also elsewhere on the board
+3V3: D4.1 (K), U6.4 (V+); also elsewhere on the board
GND: R11.2, U6.11 (V-); also elsewhere on the board
unnamed: C19.2, D4.2 (A), R11.1
unnamed 52: U6.6 (-); also elsewhere on the board
unnamed 55: U6.13 (-); also elsewhere on the board
PR-RCV-FL: U6.7; also elsewhere on the board
PR-RCV-SR: U6.14; also elsewhere on the board

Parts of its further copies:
C20, C22, C24: 22p; C_0402
C21, C23, C25: 0.01u; C_0402
D5, D6, D7: SFH213FA; Photo-5MM_Angle
R12, R14, R16: 220k; R_0402
R13, R15, R17: 100k; R_0402

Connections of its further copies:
+3V3: D5.1 (K), D6.1 (K), D7.1 (K); also elsewhere on the board
GND: R13.2, R15.2, R17.2; also elsewhere on the board
unnamed 52: C20.2, C21.1, R12.2; also elsewhere on the board
unnamed: C21.2, D5.2 (A), R13.1
unnamed: C23.2, D6.2 (A), R15.1
unnamed 55: C24.2, C25.1, R16.2; also elsewhere on the board
unnamed: C25.2, D7.2 (A), R17.1
PR-RCV-FL: C20.1, R12.1; also elsewhere on the board
PR-RCV-SR: C24.1, R16.1; also elsewhere on the board

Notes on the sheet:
IR Receiver

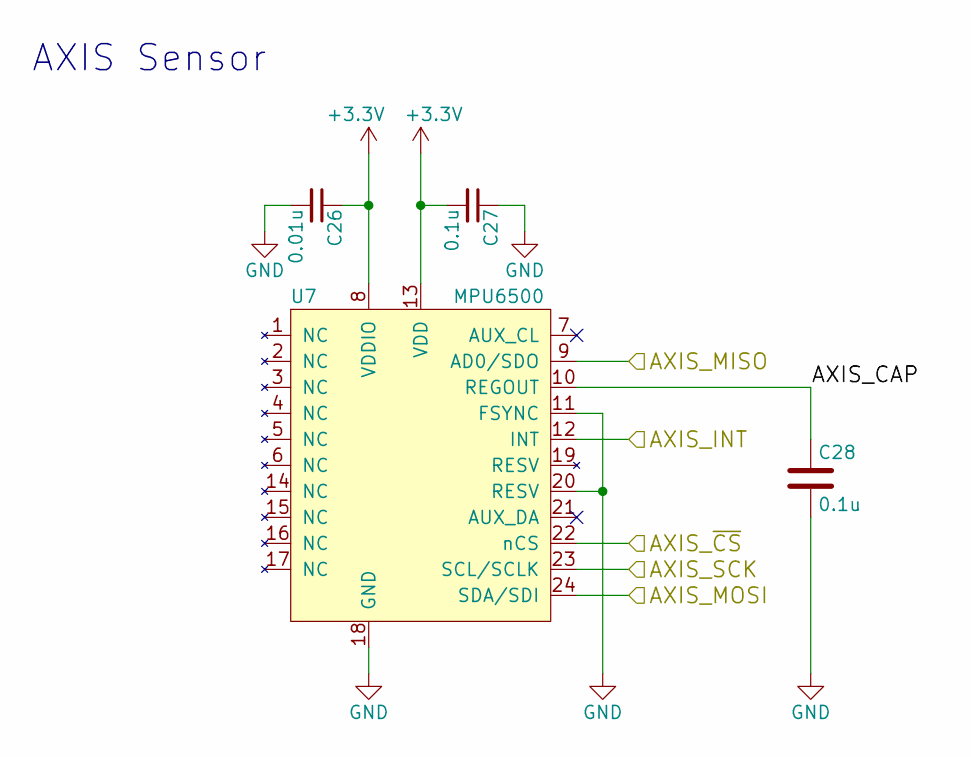
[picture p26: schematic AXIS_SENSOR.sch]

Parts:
C26: 0.01u; C_0402
C27, C28: 0.1u; C_0402
U7: MPU6500; QFN-24-1EP_3x3mm_Pitch0.4mm

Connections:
+3V3: C26.1, C27.2, U7.8 (VDDIO), U7.13 (VDD); also elsewhere on the board
/AXIS_SENSOR/AXIS_CAP: C28.1, U7.10 (REGOUT)
AXIS_INT: U7.12 (INT); also elsewhere on the board
AXIS_MISO: U7.9 (AD0/SDO); also elsewhere on the board
AXIS_MOSI: U7.24 (SDA/SDI); also elsewhere on the board
AXIS_SCK: U7.23 (SCL/SCLK); also elsewhere on the board
AXIS_~CS: U7.22 (nCS); also elsewhere on the board
GND: C26.2, C27.1, C28.2, U7.11 (FSYNC), U7.18 (GND), U7.20 (RESV); also elsewhere on the board

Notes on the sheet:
AXIS Sensor

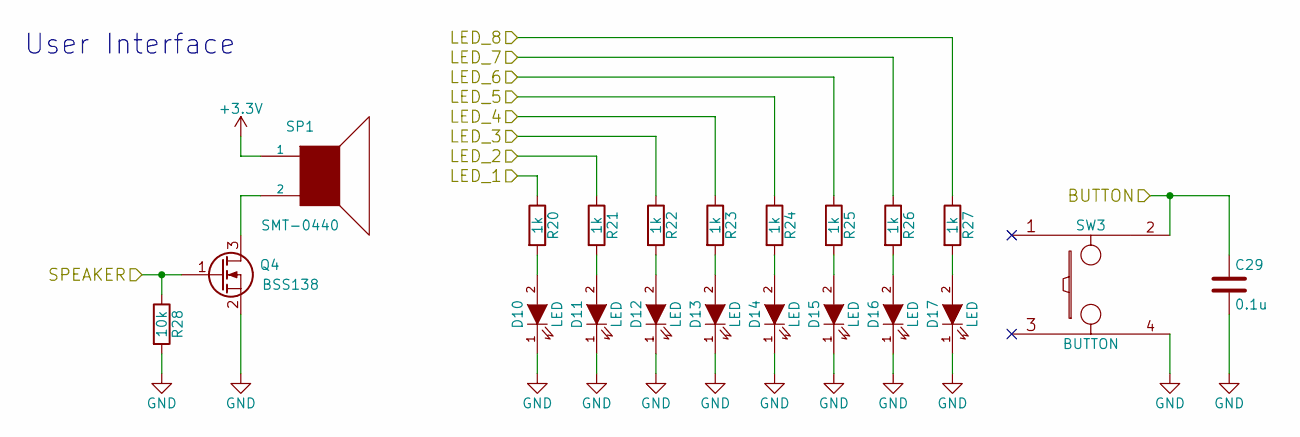
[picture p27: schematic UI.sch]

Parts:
C29: 0.1u; C_0402
D10, D11, D12, D13, D14, D15, D16, D17: LED; LED_0603
Q4: BSS138; SOT-23
R20, R21, R22, R23, R24, R25, R26, R27: 1k; R_0402
R28: 10k; R_0402
SP1: SMT-0440; SMT-0440-S-R
SW3: BUTTON; SW_PUSH

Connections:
+3V3: SP1.1; also elsewhere on the board
BUTTON: C29.1, SW3.2; also elsewhere on the board
GND: C29.2, D10.1 (K), D11.1 (K), D12.1 (K), D13.1 (K), D14.1 (K), D15.1 (K), D16.1 (K), D17.1 (K), Q4.2 (S), R28.2, SW3.4; also elsewhere on the board
LED_1: R20.1; also elsewhere on the board
LED_2: R21.1; also elsewhere on the board
LED_3: R22.1; also elsewhere on the board
LED_4: R23.1; also elsewhere on the board
LED_5: R24.1; also elsewhere on the board
LED_6: R25.1; also elsewhere on the board
LED_7: R26.1; also elsewhere on the board
LED_8: R27.1; also elsewhere on the board
unnamed: D10.2 (A), R20.2
unnamed: D11.2 (A), R21.2
unnamed: D12.2 (A), R22.2
unnamed: D13.2 (A), R23.2
unnamed: D14.2 (A), R24.2
unnamed: D15.2 (A), R25.2
unnamed: D16.2 (A), R26.2
unnamed: D17.2 (A), R27.2
unnamed: Q4.3 (D), SP1.2
SPEAKER: Q4.1 (G), R28.1; also elsewhere on the board

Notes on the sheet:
User Interface

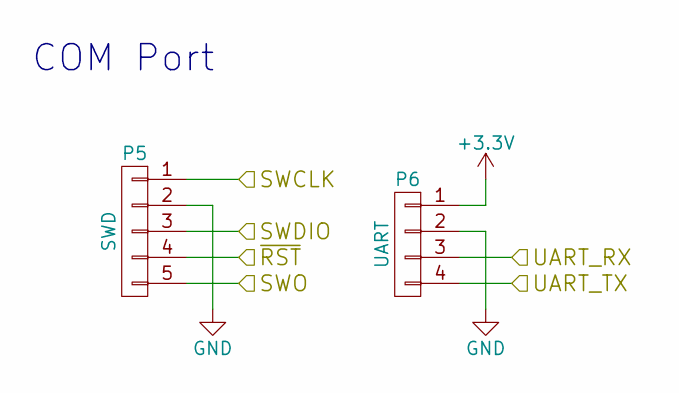
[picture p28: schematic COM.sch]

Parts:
P5: SWD; JST_SH_BM05B-SRSS-TB_05x1.00mm_Straight
P6: UART; JST_SH_BM04B-SRSS-TB_04x1.00mm_Straight

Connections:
+3V3: P6.1; also elsewhere on the board
GND: P5.2, P6.2; also elsewhere on the board
RESET: P5.4; also elsewhere on the board
SWCLK: P5.1; also elsewhere on the board
SWDIO: P5.3; also elsewhere on the board
SWO: P5.5; also elsewhere on the board
UART-RX: P6.3; also elsewhere on the board
UART-TX: P6.4; also elsewhere on the board

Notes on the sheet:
COM Port

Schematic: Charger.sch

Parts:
C30, C31, C32: 4.7u; C_0603
D18, D19: LED; LED_0603
P7: USB_A; USB_A_P
P8: BAT1; Hirose_DF13-02P-1.25DSA_02x1.25mm_Straight
P9: BAT2; Hirose_DF13-02P-1.25DSA_02x1.25mm_Straight
R29, R30: 1k; R_0603
R31, R32: 4.7k; R_0603
U8, U9: MCP73831; SOT-23-5

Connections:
/Charger A/OUT_1: C31.1, P8.1, U8.3 (VBAT)
/Charger A/OUT_2: C32.1, P9.1, U9.3 (VBAT)
/Charger A/VDD: C30.1, D18.2 (A), D19.2 (A), P7.1 (VCC), U8.4 (VDD), U9.4 (VDD)
/Charger A/VSS: C30.2, C31.2, C32.2, P7.4 (GND), P7.5 (shield), P8.2, P9.2, R31.2, R32.2, U8.2 (VSS), U9.2 (VSS)
unnamed: D18.1 (K), R29.1
unnamed: D19.1 (K), R30.1
unnamed: R29.2, U8.1 (STAT)
unnamed: R30.2, U9.1 (STAT)
unnamed: R31.1, U8.5 (PROG)
unnamed: R32.1, U9.5 (PROG)

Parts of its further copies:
C33, C34, C35: 4.7u; C_0603
D20, D21: LED; LED_0603
P10: USB_A; USB_A_P
P11: BAT1; Hirose_DF13-02P-1.25DSA_02x1.25mm_Straight
P12: BAT2; Hirose_DF13-02P-1.25DSA_02x1.25mm_Straight
R33, R34: 1k; R_0603
R35, R36: 4.7k; R_0603
U10, U11: MCP73831; SOT-23-5

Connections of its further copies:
/Charger B/OUT_1: C34.1, P11.1, U10.3 (VBAT)
/Charger B/OUT_2: C35.1, P12.1, U11.3 (VBAT)
/Charger B/VDD: C33.1, D20.2 (A), D21.2 (A), P10.1 (VCC), U10.4 (VDD), U11.4 (VDD)
/Charger B/VSS: C33.2, C34.2, C35.2, P10.4 (GND), P10.5 (shield), P11.2, P12.2, R35.2, R36.2, U10.2 (VSS), U11.2 (VSS)
unnamed: D20.1 (K), R33.1
unnamed: D21.1 (K), R34.1
unnamed: R33.2, U10.1 (STAT)
unnamed: R34.2, U11.1 (STAT)
unnamed: R35.1, U10.5 (PROG)
unnamed: R36.1, U11.5 (PROG)

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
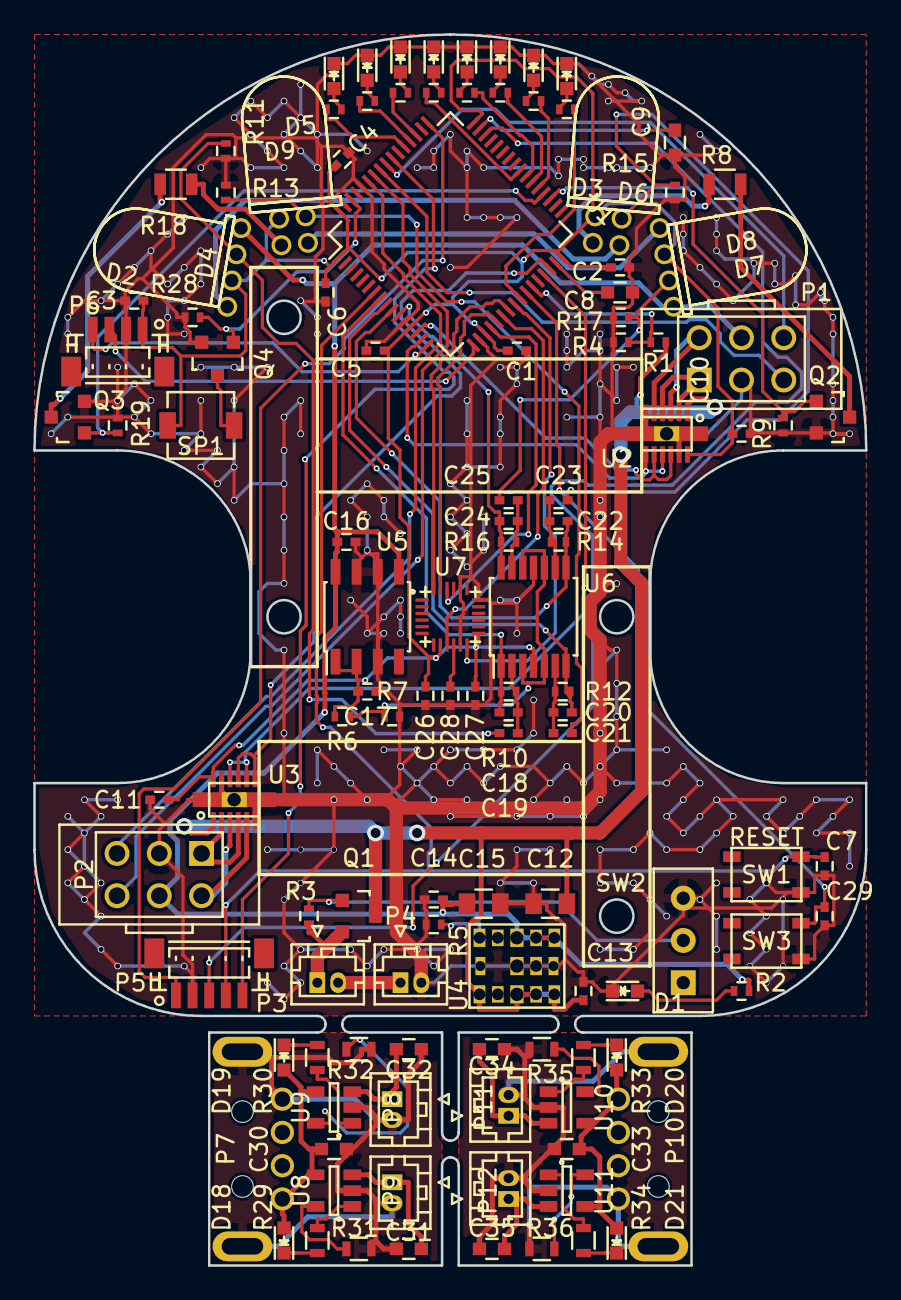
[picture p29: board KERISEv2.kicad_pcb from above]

Board: 2 copper layers, 50.0 x 74.0 mm, 123 parts (0 on the bottom side), 96 nets.

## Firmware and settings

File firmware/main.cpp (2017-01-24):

/*
 * main.cpp
 *
 *  Created on: 2016/10/23
 *      Author: kerikun11
 */

#include "mbed.h"
#include "rtos.h"

#include "config.h"
#include "Battery.h"
#include "Buzzer.h"
#include "Button.h"
#include "Motor.h"
#include "Encoder.h"
#include "MPU6500.h"
#include "Reflector.h"
#include "WallDetector.h"
#include "SpeedController.h"
#include "MoveAction.h"
#include "MazeSolver.h"

/* define each pointer */
BusOut *led;
Battery *bat;
Buzzer *bz;
Button *btn;

Motor *mt;
Encoders *enc;
MPU6500 *mpu;
Reflector *rfl;
WallDetector *wd;

SpeedController *sc;
MoveAction *ma;
MazeSolver *ms;

bool output = false;

void debug_info() {
	while (1) {
		Thread::wait(200);
//		printf("%.3f,%.3f\n", mpu->velocity.y,sc->actual.trans);

//		printf("%.3f\t%.3f\n", mpu->gyro.z * 180 / M_PI, mpu->angle.z * 180 / M_PI);
//		sc->getPosition().print();

//		printf("%05u\t%05u\t%05u\t%05u\n", rfl->sl(), rfl->fl(), rfl->fr(), rfl->sr());
//		printf("%06.3f\t%06.3f\t%06.3f\t%06.3f\n", wd->wall_difference().side[0], wd->wall_difference().front[0],
//				wd->wall_difference().front[1], wd->wall_difference().side[1]);
//		printf("%s %s %s %s\n", wd->wall().side[0] ? "X" : ".", wd->wall().front[0] ? "X" : ".",
//				wd->wall().front[1] ? "X" : ".", wd->wall().side[1] ? "X" : ".");

//		const int i = 0;
//		if (output)
//			printf("%.0f,%.0f,%.0f,%.0f,%.0f\n", sc->target.wheel[i] / 10, sc->actual.wheel[i] / 10,
//					sc->Kp * (sc->target.wheel[i] - sc->actual.wheel[i]) / 10,
//					sc->Kp * sc->Ki * (0 - sc->integral.wheel[i]) / 10,
//					sc->Kp * sc->Kd * (0 - sc->differential.wheel[i]) / 10);

//		if (output)
//			printf("%.0f,%.0f\n", sc->target.wheel[i], sc->actual.wheel[i]);
	}
}

void serial_ctrl() {
	while (1) {
		Thread::wait(100);
		int c = getchar();
		if (c == EOF)
			continue;
		printf("%c\n", (char) c);
		switch (c) {
		case 't':
			bz->play(Buzzer::CONFIRM);
			mpu->calibration();
			wd->calibration();
			break;
		case 'g':
			bz->play(Buzzer::CONFIRM);
			mpu->calibration();
			wd->calibration();
			ma->enable();
			break;
		case 'f':
			bz->play(Buzzer::CANCEL);
			ms->terminate();
			break;
		case 's':
			ma->set_action(MoveAction::START_STEP);
			bz->play(Buzzer::SELECT);
			break;
		case 'i':
			ma->set_action(MoveAction::START_INIT);
			bz->play(Buzzer::SELECT);
			break;
		case 'w':
			ma->set_action(MoveAction::GO_STRAIGHT);
			bz->play(Buzzer::SELECT);
			break;
		case 'a':
			ma->set_action(MoveAction::TURN_LEFT_90);
			bz->play(Buzzer::SELECT);
			break;
		case 'd':
			ma->set_action(MoveAction::TURN_RIGHT_90);
			bz->play(Buzzer::SELECT);
			break;
		case 'b':
			ma->set_action(MoveAction::STOP);
			bz->play(Buzzer::SELECT);
			break;
		case 'r':
			ma->set_action(MoveAction::RETURN);
			bz->play(Buzzer::SELECT);
			break;
		case 'z':
			ma->set_action(MoveAction::FAST_TURN_LEFT_90);
			bz->play(Buzzer::SELECT);
			break;
		case 'x':
			ma->set_action(MoveAction::FAST_GO_STRAIGHT);
			bz->play(Buzzer::SELECT);
			break;
		case 'c':
			ma->set_action(MoveAction::FAST_TURN_RIGHT_90);
			bz->play(Buzzer::SELECT);
			break;
		case 'u':
			ms->terminate();
			ma->set_action(MoveAction::START_STEP);
			for (int i = 0; i < 5; i++) {
				ma->set_action(MoveAction::TURN_RIGHT_90);
				ma->set_action(MoveAction::TURN_RIGHT_90);
				ma->set_action(MoveAction::RETURN);
				ma->set_action(MoveAction::TURN_LEFT_90);
				ma->set_action(MoveAction::TURN_LEFT_90);
				ma->set_action(MoveAction::RETURN);
			}
			ma->set_action(MoveAction::TURN_RIGHT_90);
			ma->set_action(MoveAction::TURN_RIGHT_90);
			ma->set_action(MoveAction::RETURN);
			ma->set_action(MoveAction::TURN_LEFT_90);
			ma->set_action(MoveAction::TURN_LEFT_90);
			ma->set_action(MoveAction::START_INIT);
			bz->play(Buzzer::CONFIRM);
			mpu->calibration();
			wd->calibration();
			ma->enable();
			break;
		case 'm':
			bz->play(Buzzer::CONFIRM);
			ms->terminate();
			ms->start();
			break;
		case 'p':
			bz->play(Buzzer::SELECT);
			printf("%05u\t%05u\t%05u\t%05u\n", rfl->sl(), rfl->fl(), rfl->fr(), rfl->sr());
			printf("%06.3f\t%06.3f\t%06.3f\t%06.3f\n", wd->wall_difference().side[0], wd->wall_difference().front[0],
					wd->wall_difference().front[1], wd->wall_difference().side[1]);
			printf("%s %s %s %s\n", wd->wall().side[0] ? "X" : ".", wd->wall().front[0] ? "X" : ".",
					wd->wall().front[1] ? "X" : ".", wd->wall().side[1] ? "X" : ".");
			printf("Position:\t(%06.1f, %06.1f, %06.3f)\n", sc->getPosition().x, sc->getPosition().y,
					sc->getPosition().theta);
			break;
		}
	}
}

void emergencyTask() {
	while (1) {
		Thread::wait(1);
		if (fabs(mpu->accel.y) > 9800 * 8 || fabs(mpu->gyro.z) > 10 * M_PI) {
			mt->emergency_stop();
			ms->terminate();
			bz->play(Buzzer::EMERGENCY);
			while (mt->isEmergency()) {
				*led = 0xAA;
				Thread::wait(100);
				*led = 0x55;
				Thread::wait(100);
			}
		}
	}
}

int main() {
	/* make instances */
	led = new BusOut(LED1_PIN, LED2_PIN, LED3_PIN, LED4_PIN, LED5_PIN, LED6_PIN, LED7_PIN, LED8_PIN);
	bat = new Battery(BATTERY_PIN);
	bz = new Buzzer(BUZZER_PIN);
	btn = new Button(BUTTON_PIN);

	mt = new Motor;

	enc = new Encoders(ENCODER_L_TIMx, ENCODER_R_TIMx);
	mpu = new MPU6500(MPU6500_MOSI_PIN, MPU6500_MISO_PIN, MPU6500_SCLK_PIN, MPU6500_SSEL_PIN);

	rfl = new Reflector(IR_LED_SL_FR_PIN, IR_LED_SR_FL_PIN);
	wd = new WallDetector(rfl);

	sc = new SpeedController(mt, enc, mpu);
	ma = new MoveAction(bz, mt, enc, mpu, rfl, wd, sc);
	ms = new MazeSolver(bz, mpu, rfl, ma, wd);

	/* boot */
	{
		printf("\nHello World!\n");
		printf("Battery Voltage: %.3f [V]\n", bat->voltage());
		if (!bat->check()) {
			bz->play(Buzzer::LOW_BATTERY);
			printf("Battery Low!\n");
			while (1) {
				Thread::wait(10);
				if (btn->pressed) {
					btn->flags = 0;
					break;
				}
			}
		}
		bz->play(Buzzer::BOOT);
		int gage = bat->gage(9);
		for (int i = 0; i < gage; i++)
			(*led)[i] = 1;
		Thread::wait(1000);
		*led = 0;
	}

	/* for debug */
	Thread debugInfoThread(PRIORITY_DEBUG_INFO, STACK_SIZE_DEBUG_INFO);
	debugInfoThread.start(debug_info);
	Thread serialCtrlThread(PRIORITY_SERIAL_CTRL, STACK_SIZE_SERIAL_CTRL);
	serialCtrlThread.start(serial_ctrl);
	Thread emergencyThread(PRIORITY_EMERGENCY_STOP, STACK_SIZE_EMERGENCY);
	emergencyThread.start(emergencyTask);

//	while (1) {
//		while (1) {
//			Thread::wait(10);
//			if (btn->pressed) {
//				btn->flags = 0;
//				bz->play(Buzzer::CONFIRM);
//				break;
//			}
//		}
//		Thread::wait(1000);
//		sc->enable();
//		output = true;
//		sc->set_target(600, 0);
//		Thread::wait(400);
//		sc->set_target(0, 0);
//		Thread::wait(400);
//		output = false;
//		sc->disable();
//	}

	int mode = 0;
	while (true) {
		Thread::wait(10);
		while (mt->isEmergency()) {
			Thread::wait(10);
			if (btn->pressed) {
				btn->flags = 0;
				bz->play(Buzzer::BOOT);
				mt->emergency_release();
				*led = 0;
				printf("Released Emergency\n");
			}
		}
		while (ma->actions()) {
			Thread::wait(10);
			if (btn->pressed) {
				btn->flags = 0;
				bz->play(Buzzer::CANCEL);
				ms->terminate();
			}
		}
		if (btn->pressed) {
			btn->flags = 0;
			bz->play(Buzzer::CONFIRM);
			while (1) {
				Thread::wait(100);
				mode = enc->position() / 2;
				mode &= 0xF;
				*led = mode;
				if (btn->pressed) {
					btn->flags = 0;
					bz->play(Buzzer::CONFIRM);
					break;
				}
			}
			rfl->enable();
			while (1) {
				Thread::wait(10);
				if (rfl->front(0) > 400 && rfl->front(1) > 400) {
					bz->play(Buzzer::CONFIRM);
					Thread::wait(200);
					switch (mode) {
					case 0:
						ms->terminate();
						ms->start();
						break;
					case 1:
						ms->terminate();
						ma->set_action(MoveAction::START_STEP);
						for (int i = 0; i < 2; i++) {
							ma->set_action(MoveAction::TURN_RIGHT_90);
							ma->set_action(MoveAction::TURN_RIGHT_90);
							ma->set_action(MoveAction::RETURN);
							ma->set_action(MoveAction::TURN_LEFT_90);
							ma->set_action(MoveAction::TURN_LEFT_90);
							ma->set_action(MoveAction::RETURN);
						}
						ma->set_action(MoveAction::TURN_RIGHT_90);
						ma->set_action(MoveAction::TURN_RIGHT_90);
						ma->set_action(MoveAction::RETURN);
						ma->set_action(MoveAction::TURN_LEFT_90);
						ma->set_action(MoveAction::TURN_LEFT_90);
						ma->set_action(MoveAction::START_INIT);
						mpu->calibration();
						wd->calibration();
						ma->enable();
						break;
					case 2:
						ma->set_action(MoveAction::FAST_GO_STRAIGHT);
						for (int i = 0; i < 4; i++) {
							ma->set_action(MoveAction::FAST_GO_STRAIGHT, 6);
							ma->set_action(MoveAction::FAST_TURN_RIGHT_90);
							ma->set_action(MoveAction::FAST_TURN_RIGHT_90);
							ma->set_action(MoveAction::FAST_GO_STRAIGHT, 6);
							ma->set_action(MoveAction::FAST_TURN_RIGHT_90);
							ma->set_action(MoveAction::FAST_TURN_RIGHT_90);
						}
						mpu->calibration();
						wd->calibration();
						ma->enable();
						break;
					case 3:
						ma->set_action(MoveAction::FAST_GO_STRAIGHT);
						ma->set_action(MoveAction::FAST_GO_STRAIGHT, 9);
						ma->set_action(MoveAction::FAST_GO_HALF);
						ma->set_action(MoveAction::FAST_TURN_RIGHT_180);
						ma->set_action(MoveAction::FAST_GO_HALF);
						ma->set_action(MoveAction::FAST_GO_STRAIGHT, 9);
						mpu->calibration();
						wd->calibration();
						ma->enable();
						break;
					case 4:
						ma->set_action(MoveAction::FAST_GO_STRAIGHT);
						ma->set_action(MoveAction::FAST_GO_STRAIGHT);
						ma->set_action(MoveAction::FAST_TURN_RIGHT_150);
						ma->set_action(MoveAction::FAST_TURN_LEFT_120);
						ma->set_action(MoveAction::FAST_TURN_RIGHT_120);
						ma->set_action(MoveAction::FAST_TURN_LEFT_120);
						ma->set_action(MoveAction::FAST_TURN_RIGHT_150R);
						ma->set_action(MoveAction::FAST_GO_STRAIGHT);
						mpu->calibration();
						wd->calibration();
						ma->enable();
						break;
					}
					break;
				}
				if (btn->pressed) {
					btn->flags = 0;
					bz->play(Buzzer::CANCEL);
					ms->terminate();
					rfl->disable();
					break;
				}
			}
		}
	}
}

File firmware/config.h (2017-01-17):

/*
 * config.h
 *
 *  Created on: 2016/10/23
 *      Author: kerikun11
 */

#ifndef CONFIG_H_
#define CONFIG_H_

#include "mbed.h"

/* Thread Priorities */

#define PRIORITY_REFLECTOR_UPDATE	osPriorityHigh
#define PRIORITY_MPU6500_UPDATE		osPriorityHigh

#define PRIORITY_WALL_UPDATE		osPriorityAboveNormal
#define PRIORITY_ENCODER_UPDATE		osPriorityAboveNormal

#define PRIORITY_EMERGENCY_STOP		osPriorityAboveNormal
#define PRIORITY_SPEED_CONTROLLER	osPriorityAboveNormal

#define PRIORITY_MOVE_ACTION		osPriorityNormal
#define PRIORITY_BUZZER				osPriorityNormal

#define PRIORITY_MAZE_SOLVER		osPriorityBelowNormal

#define PRIORITY_DEBUG_INFO			osPriorityLow

#define PRIORITY_SERIAL_CTRL		osPriorityIdle

/* thread stack size */

#define STACK_SIZE_BUZZER			1024
#define STACK_SIZE_ENCODER			512
#define STACK_SIZE_MAZE_SOLVER		4096
#define STACK_SIZE_MOVE_ACTION		4096
#define STACK_SIZE_MPU6500_UPDATE	1024
#define STACK_SIZE_REFLECTOR_UPDATE	512
#define STACK_SIZE_SPEED_CONTROLLER	1024
#define STACK_SIZE_WALL_UPDATE		512
#define STACK_SIZE_DEBUG_INFO		2048
#define STACK_SIZE_SERIAL_CTRL		2048
#define STACK_SIZE_EMERGENCY		512

/* Maze Size */
#define HALF_SIZE					true

#if HALF_SIZE
#define SEGMENT_WIDTH				90
#define WALL_THICKNESS				6
#else
#define SEGMENT_WIDTH				180
#define WALL_THICKNESS				12
#endif

/* Hardware Parameter */

#define MACHINE_TAIL_LENGTH			24.0f
#define MACHINE_ROTATION_RADIUS		21.5f
#define WHEEL_DIAMETER_MM			24.5f
#define WHEEL_GEER_RATIO			0.25f
#define ENCODER_PULSES				(1024*4)

/* Calibration Parameter */

#if HALF_SIZE

#define SPEED_CONTROLLER_KP			1.6f
#define SPEED_CONTROLLER_KI			24.0f
#define SPEED_CONTROLLER_KD			0.001f

#define WALL_DETECTOR_FLONT_RATIO	1.0f
#define WALL_SIDE_DIV				4
#define WALL_FRONT_DIV				9

#else

#define SPEED_CONTROLLER_KP			1.8f
#define SPEED_CONTROLLER_KI			24.0f
#define SPEED_CONTROLLER_KD			0.001f

#define WALL_DETECTOR_FLONT_RATIO	1.0f
#define WALL_SIDE_DIV				3
#define WALL_FRONT_DIV				6

#endif

/* Update/Sampling Period [us] */

#define MPU6500_UPDATE_PERIOD_US	1000

#define ENCODER_UPDATE_PERIOD_US	1000

#define IR_LED_PERIOD_US				200
#define IR_LED_DUTY_US					100
#define IR_RECEIVER_SAMPLE_SIZE			25
#define IR_RECEIVER_SAMPLING_PERIOD_US	20
#define IR_RECEIVER_UPDATE_PERIOD_US	1000

#define WALL_UPDATE_PERIOD_US		1000

#define SPEED_CONTROLLER_PERIOD_US	1000

#define MOVE_ACTION_PERIOD			1000

/* Pin Mapping */

#define BATTERY_PIN					PB_1

#define BUZZER_PIN					PB_9	//< Modify PeripheralPins.c PWM Pin using Timer11

#define BUTTON_PIN					PB_0

#define LED1_PIN					PC_5
#define LED2_PIN					PC_6
#define LED3_PIN					PC_7
#define LED4_PIN					PC_8
#define LED5_PIN					PC_9
#define LED6_PIN					PC_10
#define LED7_PIN					PC_11
#define LED8_PIN					PC_12

#define MPU6500_MOSI_PIN			PA_7
#define MPU6500_MISO_PIN			PA_6
#define MPU6500_SCLK_PIN			PA_5
#define MPU6500_SSEL_PIN			PA_4

#define IR_LED_SL_FR_PIN			PB_14
#define IR_LED_SR_FL_PIN			PB_15

/* Motor */
#define MOTOR_TIMx						TIM2
#define MOTOR_TIMx_CLK_ENABLE()			__HAL_RCC_TIM2_CLK_ENABLE()
#define MOTOR_TIMx_CHANNEL_GPIO_PORT()	do{__HAL_RCC_GPIOA_CLK_ENABLE();__HAL_RCC_GPIOB_CLK_ENABLE();}while(0)
#define MOTOR_TIMx_GPIO_PORT_CHANNEL1	GPIOA
#define MOTOR_TIMx_GPIO_PORT_CHANNEL2	GPIOA
#define MOTOR_TIMx_GPIO_PORT_CHANNEL3	GPIOB
#define MOTOR_TIMx_GPIO_PORT_CHANNEL4	GPIOB
#define MOTOR_TIMx_GPIO_PIN_CHANNEL1	GPIO_PIN_0
#define MOTOR_TIMx_GPIO_PIN_CHANNEL2	GPIO_PIN_1
#define MOTOR_TIMx_GPIO_PIN_CHANNEL3	GPIO_PIN_10
#define MOTOR_TIMx_GPIO_PIN_CHANNEL4	GPIO_PIN_11
#define MOTOR_TIMx_GPIO_AF_CHANNEL		GPIO_AF1_TIM2
#define MOTOR_PERIOD_VALUE				(1000 - 1)

/* Encoder */
#define ENCODER_L_TIMx	TIM3
#define ENCODER_R_TIMx	TIM4

/* Definition for ADCx clock resources */
#define ADCx_S							ADC2
#define ADCx_F							ADC3
#define ADCx_S_CLK_ENABLE()				__HAL_RCC_ADC2_CLK_ENABLE()
#define ADCx_F_CLK_ENABLE()				__HAL_RCC_ADC3_CLK_ENABLE()
#define ADCx_CHANNEL_GPIO_CLK_ENABLE()  __HAL_RCC_GPIOC_CLK_ENABLE()

#define ADCx_FORCE_RESET()              __HAL_RCC_ADC_FORCE_RESET()
#define ADCx_RELEASE_RESET()            __HAL_RCC_ADC_RELEASE_RESET()

/* Definition for ADCx Channel Pin */
#define ADCx_CHANNEL_SL_PIN             GPIO_PIN_0
#define ADCx_CHANNEL_FL_PIN             GPIO_PIN_1
#define ADCx_CHANNEL_FR_PIN             GPIO_PIN_2
#define ADCx_CHANNEL_SR_PIN             GPIO_PIN_3
#define ADCx_CHANNEL_GPIO_PORT          GPIOC

/* Definition for ADCx's Channel */
#define ADCx_CHANNEL_SL					ADC_CHANNEL_10
#define ADCx_CHANNEL_FL					ADC_CHANNEL_11
#define ADCx_CHANNEL_FR					ADC_CHANNEL_12
#define ADCx_CHANNEL_SR					ADC_CHANNEL_13

/*
 * TIM1		IR LED
 * TIM2		mbed timer
 * TIM3		Encoder L
 * TIM4		Encoder R
 * TIM5		*
 * TIM6		*
 * TIM7		*
 * TIM8		*
 * TIM9		*
 * TIM10	*
 * TIM11	Buzzer
 * TIM12	*
 * TIM13	*
 * TIM14	*
 */
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

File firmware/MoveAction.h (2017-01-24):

/*
 * MoveAction.h
 *
 *  Created on: 2016/11/11
 *      Author: kerikun11
 */

#ifndef MOVEACTION_H_
#define MOVEACTION_H_

#include "mbed.h"
#include "config.h"
#include <vector>
#include <queue>
#include <string>

#define WALL_ATTACH_ENABLED			false
#define WALL_AVOID_ENABLED			true

#if HALF_SIZE
#define LOOK_AHEAD_UNIT				3
#define TRAJECTORY_PROP_GAIN		80
#define TRAJECTORY_INT_GAIN			0
#define WALL_AVOID_GAIN				0.0001f
#else
#define LOOK_AHEAD_UNIT				6
#define TRAJECTORY_PROP_GAIN		40
#define TRAJECTORY_INT_GAIN			0
#endif

class Trajectory {
public:
	Trajectory() {
		reset();
	}
	virtual ~Trajectory() {
	}
	void reset() {
		last_index = 0;
	}
	Position getNextDir(const Position &cur, float velocity) {
		int index_cur = getNextIndex(cur);
		int look_ahead = LOOK_AHEAD_UNIT * (1.0f + pow(velocity / 600, 2));
		Position dir = (getPosition(index_cur + look_ahead) - cur).rotate(-cur.theta);
		dir.theta = atan2f(dir.y, dir.x);
		return dir;
	}
	float getRemain() const {
		return (getSize() - last_index) * interval;
	}
	Position getEndPosition() {
		return getPosition(getSize());
	}
protected:
	int last_index;
	const float interval = 2.0f;
	virtual int size() const {
		return 180;
	}
	virtual Position position(int index) const {
		return Position(index * interval, 0, 0);
	}
	int getSize() const {
		return size();
	}
	Position getPosition(const int index) {
		return position(index);
	}
	int getNextIndex(const Position& pos) {
		for (int i = last_index;; i++) {
			Position target = getPosition(i);
			Position dir = (target - pos).rotate(-target.theta);
			if (dir.x > 0) {
				last_index = i;
				return last_index;
			}
		}
		return last_index;
	}
};

#if HALF_SIZE

class Curve90: public Trajectory {
public:
	Curve90(bool mirror = false) :
			Trajectory(), mirror(mirror) {
	}
	const float velocity = 260.0f;
	const float straight = 15.0f;
private:
	bool mirror;
	virtual int size() const {
		return 26;
	}
	virtual Position position(int index) const {
		static const float data[26 + 1][3] =
				{ { 0.0000000000, 0.0000000000, 0.0000000000 }, { 1.9999999343, 0.0003581351, 0.0007153325 }, { 3.9999907677, 0.0056854550, 0.0056557394 }, { 5.9998473365, 0.0284088519, 0.0187172793 }, { 7.9989048295, 0.0881534668, 0.0431636004 }, { 9.9950574894, 0.2101682305, 0.0813717929 }, { 11.9834416379, 0.4231979224, 0.1346472802 }, { 13.9550171391, 0.7568522412, 0.2031221621 }, { 15.8955471785, 1.2385834025, 0.2857449285 }, { 17.7855147928, 1.8905302360, 0.3803623424 }, { 19.6013550216, 2.7266811121, 0.4838871173 }, { 21.3180252310, 3.7509398130, 0.5925383310 }, { 22.9124075718, 4.9567247722, 0.7024742720 }, { 24.3648619081, 6.3301689163, 0.8124179843 }, { 25.6578492022, 7.8546872908, 0.9223616965 }, { 26.7758327680, 9.5118234214, 1.0320459270 }, { 27.7078174774, 11.2803284795, 1.1386823358 }, { 28.4522831355, 13.1357157330, 1.2382647117 }, { 29.0182522779, 15.0532748985, 1.3273191357 }, { 29.4240311767, 17.0111878431, 1.4031915235 }, { 29.6947572836, 18.9924659652, 1.4642543049 }, { 29.8593376545, 20.9855072002, 1.5100331663 }, { 29.9473142489, 22.9834898549, 1.5412439863 }, { 29.9860126781, 24.9830869308, 1.5597370888 }, { 29.9981501834, 26.9830439783, 1.5683531544 }, { 29.9999745380, 28.9830427265, 1.5707020100 }, { 30.0000000000, 30.0000000059, 1.5707963268 }, };
		Position ret;
		if (index < 0) {
			ret = Position(0 + interval * index, 0, 0);
		} else if (index > size() - 1) {
			Position end(data[size()][0], data[size()][1], data[size()][2]);
			ret = end
					+ Position((index - size()) * interval * cos(end.theta),
							(index - size()) * interval * sin(end.theta), 0);
		} else {
			ret = Position(data[index][0], data[index][1], data[index][2]);
		}
		if (mirror)
			return ret.mirror_x();
		return ret;
	}
};

class C30: public Trajectory {
public:
	C30(bool mirror = false) :
			Trajectory(), mirror(mirror) {
	}
	const float velocity = 761.5056368240381;
private:
	bool mirror;
	virtual int size() const {
		return 33;
	}
	virtual Position position(int index) const {
		static const float data[33 + 1][3] =
				{ { 0.0000000000, 0.0000000000, 0.0000000000 }, { 1.9999999986, 0.0000502581, 0.0001004536 }, { 3.9999998169, 0.0008011255, 0.0007991263 }, { 5.9999969173, 0.0040304778, 0.0026719061 }, { 7.9999773716, 0.0126275827, 0.0062508522 }, { 9.9998948870, 0.0304850952, 0.0120043334 }, { 11.9996352112, 0.0623531676, 0.0203195445 }, { 13.9989665875, 0.1136605100, 0.0314880521 }, { 15.9974804901, 0.1903081559, 0.0456949109 }, { 17.9945300480, 0.2984425368, 0.0630117555 }, { 19.9891758083, 0.4442153936, 0.0833941265 }, { 21.9801493466, 0.6335391051, 0.1066831300 }, { 23.9658444537, 0.8718471322, 0.1326113691 }, { 25.9443431852, 1.1638702507, 0.1608129257 }, { 27.9134801831, 1.5134397327, 0.1908370198 }, { 29.8709438578, 1.9233282844, 0.2221648374 }, { 31.8144079321, 2.3951380854, 0.2542288968 }, { 33.7416822788, 2.9292426264, 0.2864342331 }, { 35.6508686661, 3.5247854008, 0.3181806074 }, { 37.5405055286, 4.1797343225, 0.3488849138 }, { 39.4096864645, 4.8909866270, 0.3780029461 }, { 41.2581397367, 5.6545156125, 0.4050497129 }, { 43.0862602190, 6.4655484034, 0.4296175421 }, { 44.8950903243, 7.3187632191, 0.4513912987 }, { 46.6862517485, 8.2084953458, 0.4701601493 }, { 48.4618346500, 9.1289427965, 0.4858254319 }, { 50.2242546243, 10.0743649553, 0.4984043388 }, { 51.9760901761, 11.0392697698, 0.5080292754 }, { 53.7199142065, 12.0185867809, 0.5149429169 }, { 55.4581323950, 13.0078241819, 0.5194891500 }, { 57.1928394398, 14.0032081254, 0.5221002350 }, { 58.9257012620, 15.0018018568, 0.5232806708 }, { 60.6578678534, 16.0016012708, 0.5235883613 }, { 61.4711431703, 16.4711431703, 0.5235987756 }, };
		Position ret;
		if (index < 0) {
			ret = Position(0 + interval * index, 0, 0);
		} else if (index > size() - 1) {
			Position end(data[size()][0], data[size()][1], data[size()][2]);
			ret = end
					+ Position((index - size()) * interval * cos(end.theta),
							(index - size()) * interval * sin(end.theta), 0);
		} else {
			ret = Position(data[index][0], data[index][1], data[index][2]);
		}
		if (mirror)
			return ret.mirror_x();
		return ret;
	}
};
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

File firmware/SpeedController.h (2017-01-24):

/*
 * SpeedController.h
 *
 *  Created on: 2016/10/28
 *      Author: kerikun11
 */

#ifndef SPEEDCONTROLLER_H_
#define SPEEDCONTROLLER_H_

#include "mbed.h"
#include "config.h"

class Position {
public:
	Position(const float x = 0, const float y = 0, const float theta = 0) :
			x(x), y(y), theta(theta) {
	}
	Position(const float pos[3]) :
			x(pos[0]), y(pos[1]), theta(pos[2]) {
	}
	float x, y, theta;

	inline void reset() {
		x = 0;
		y = 0;
		theta = 0;
	}
	inline void set(const float x = 0, const float y = 0, const float theta = 0) {
		this->x = x;
		this->y = y;
		this->theta = theta;
	}
	inline Position rotate(const float angle) {
		float _x = x;
		float _y = y;
		x = _x * cos(angle) - _y * sin(angle);
		y = _x * sin(angle) + _y * cos(angle);
		return *this;
	}
	inline float getNorm() const {
		return sqrt(x * x + y * y);
	}
	inline Position mirror_x() const {
		return Position(x, -y, -theta);
	}
	inline Position operator=(const Position &obj) {
		x = obj.x;
		y = obj.y;
		theta = obj.theta;
		return *this;
	}
	inline Position operator+() const {
		return Position(x, y, theta);
	}
	inline Position operator+(const Position &obj) const {
		return Position(x + obj.x, y + obj.y, theta + obj.theta);
	}
	inline Position operator+=(const Position &obj) {
		x += obj.x;
		y += obj.y;
		theta += obj.theta;
		return *this;
	}
	inline Position operator-() const {
		return Position(-x, -y, -theta);
	}
	inline Position operator-(const Position &obj) const {
		return Position(x - obj.x, y - obj.y, theta - obj.theta);
	}
	inline Position operator-=(const Position &obj) {
		x -= obj.x;
		y -= obj.y;
		theta -= obj.theta;
		return *this;
	}
	inline Position operator/(const float &div) {
		return Position(x / div, y / div, theta);
	}
	inline Position operator/=(const float &div) {
		x /= div;
		y /= div;
		return *this;
	}
	inline Position operator*(const float &div) {
		return Position(x * div, y * div, theta);
	}
	inline Position operator*=(const float &div) {
		x *= div;
		y *= div;
		return *this;
	}
	inline void print(const char* name = "") {
		printf("%s: (%.1f,\t%.1f,\t%.3f)\n", name, x, y, theta);
	}
};

class SpeedController {
public:
	SpeedController(Motor *mt, Encoders *enc, MPU6500 *mpu) :
			mt(mt), enc(enc), mpu(mpu), ctrlThread(PRIORITY_SPEED_CONTROLLER,
			STACK_SIZE_SPEED_CONTROLLER) {
		ctrlThread.start(this, &SpeedController::ctrlTask);
		for (int i = 0; i < 2; i++) {
			target.wheel[i] = 0;
			for (int j = 0; j < 3; j++) {
				wheel_position[j][i] = enc->position(i);
			}
			actual.wheel[i] = 0;
			integral.wheel[i] = 0;
			differential.wheel[i] = 0;
		}
		actual_prev.trans = 0;
		actual_prev.rot = 0;
	}
	struct WheelParameter {
		WheelParameter(float trans = 0, float rot = 0) :
				trans(trans), rot(rot) {
		}
		float trans;	//< translation
		float rot;		//< rotation
		float wheel[2];	//< wheel [0]: left, [1]: right
		void pole2wheel() {
			wheel[0] = trans - MACHINE_ROTATION_RADIUS * rot;
			wheel[1] = trans + MACHINE_ROTATION_RADIUS * rot;
		}
		void wheel2pole() {
			rot = (wheel[1] - wheel[0]) / 2.0f / MACHINE_ROTATION_RADIUS;
			trans = (wheel[1] + wheel[0]) / 2.0f;
		}
	};
	void enable() {
		disable();
		for (int i = 0; i < 2; i++) {
			target.wheel[i] = 0;
			for (int j = 0; j < 3; j++) {
				wheel_position[j][i] = enc->position(i);
			}
			actual.wheel[i] = 0;
			integral.wheel[i] = 0;
			differential.wheel[i] = 0;
		}
		actual_prev.trans = 0;
		actual_prev.rot = 0;
		ctrlTicker.attach_us(this, &SpeedController::ctrlIsr,
		SPEED_CONTROLLER_PERIOD_US);
		printf("Speed Controller Enabled\n");
	}
	void disable() {
		ctrlTicker.detach();
		mt->free();
	}
	void set_target(float trans, float rot) {
		target.trans = trans;
		target.rot = rot;
		target.pole2wheel();
	}
	Position& getPosition() {
		return position;
	}
	WheelParameter target;
	WheelParameter actual;
	WheelParameter integral;
	WheelParameter differential;
	const float Kp = SPEED_CONTROLLER_KP;
	const float Ki = SPEED_CONTROLLER_KI;
	const float Kd = SPEED_CONTROLLER_KD;
private:
	Motor *mt;
	Encoders *enc;
	MPU6500 *mpu;
	Thread ctrlThread;
	Ticker ctrlTicker;
	float wheel_position[3][2];
	WheelParameter actual_prev;
	Position position;

	void ctrlIsr() {
		ctrlThread.signal_set(0x01);
	}
	void ctrlTask() {
		while (1) {
			Thread::signal_wait(0x01);
			for (int i = 0; i < 2; i++) {
				wheel_position[2][i] = wheel_position[1][i];
				wheel_position[1][i] = wheel_position[0][i];
				wheel_position[0][i] = enc->position(i);
			}
			for (int i = 0; i < 2; i++) {
				actual.wheel[i] = (wheel_position[0][i] - wheel_position[1][i]) * 1000000 / SPEED_CONTROLLER_PERIOD_US;
			}
			actual.wheel2pole();
//			actual.trans = mpu->velocity.y;
			actual.rot = mpu->gyro.z;
			actual.pole2wheel();
			for (int i = 0; i < 2; i++) {
				integral.wheel[i] += (actual.wheel[i] - target.wheel[i]) * SPEED_CONTROLLER_PERIOD_US / 1000000;
			}
			differential.wheel2pole();
			differential.trans = mpu->accel.y;
			differential.rot = 0;
			differential.pole2wheel();
			float pwm_value[2];
			for (int i = 0; i < 2; i++) {
				pwm_value[i] = Kp * (target.wheel[i] - actual.wheel[i]) + Kp * Ki * (0 - integral.wheel[i])
						+ Kp * Kd * (0 - differential.wheel[i]);
			}
			mt->drive(pwm_value[0], pwm_value[1]);

			position.theta += (actual_prev.rot + actual.rot) / 2 * SPEED_CONTROLLER_PERIOD_US / 1000000;
			position.x += (actual_prev.trans + actual.trans) / 2 * cos(position.theta) * SPEED_CONTROLLER_PERIOD_US
					/ 1000000;
			position.y += (actual_prev.trans + actual.trans) / 2 * sin(position.theta) * SPEED_CONTROLLER_PERIOD_US
					/ 1000000;

			actual_prev.trans = actual.trans;
			actual_prev.rot = actual.rot;
		}
	}
};

#endif /* SPEEDCONTROLLER_H_ */

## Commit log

2016-11-24 外形を作成
    [6AXIS_SENSOR.sch, AXIS_SENSOR.sch, COM.sch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]
2016-11-24 大きめの部品を配置
    [Mouse-01.kicad_pcb]
2016-11-25 フットプリント調整
    [IR_LED.sch, IR_RCV.sch, Motor.sch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]
2016-11-25 徐々に部品を配置，部品の確認
    [AXIS_SENSOR.sch, COM.sch, IR_LED.sch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]
2016-11-26 とりあえず全部品を配置
    [COM.sch, IR_LED.sch, IR_RCV.sch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]
2016-11-26 ネットリストとデザインルールを更新
    [Mouse-01.dsn, Power.sch]
2016-11-27 ネットリストを更新
    [IR_RCV.sch, Mouse-01.dsn, Mouse-01.kicad_pcb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]
2016-11-27 IR LEDとフォトダイオードのフットプリントを更新．
    かなりすっきり収まった．
    [Mouse-01.kicad_pcb]
2016-11-30 部品表を作成
    [Mouse-01.csv, Mouse-01.xlsx]
2016-11-30 部品の位置を調整，ロゴを貼り付け
    [Mouse-01.dsn, Mouse-01.kicad_pcb]
2016-12-01 自動配線へ出力
    [Mouse-01.dsn, Mouse-01.kicad_pcb]
2016-12-02 リポ充電基板を追加
    [AXIS_SENSOR.sch, COM.sch, Charger.sch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]
2016-12-02 充電基板を階層に．
    [AXIS_SENSOR.sch, COM.sch, Charger.sch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]
2016-12-02 自動配線Postroute
    [Mouse-01.csv, Mouse-01.dsn, Mouse-01.kicad_pcb]
2016-12-03 自動配線結果を反映
    [Mouse-01.kicad_pcb]
2016-12-03 viaを量産
    [Mouse-01.kicad_pcb]
2016-12-03 ガーバーを生成
    [Mouse-01-B.Cu.gbl, Mouse-01-B.Mask.gbs, Mouse-01-B.SilkS.gbo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]
2016-12-03 ファイル名を変更，整理
    [AXIS_SENSOR.sch, COM.sch, Charger.sch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]
2016-12-03 基板発注
    [-4digree.stl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]
2016-12-06 基板やマウンタの画像を追加
2016-12-18 MicroMouse2016のfirmwareを移植
2016-12-20 PIパラメータの調整，ログの出力
2016-12-20 ログの解除
2016-12-21 MPU6500の読み取り部分を整理．6軸を読み取り．
2016-12-21 PIDパラメータを再調整
2016-12-22 WallAttachのバグ修正
    x修正時に回転するのを忘れていた．
2016-12-23 PCなしでジグザグなどのデモを行えるようにした
2016-12-24 MPUを台形積分
2016-12-25 積分とキャリブレーションのバグを修正，加速度を[mm]単位に変換
2016-12-25 -45度入45度出を実装
2016-12-26 パラメータの調整
2016-12-26 デバック出力を削除
2016-12-26 新基板，部品を配置
    [COM.sch, Charger.sch, IR_LED.sch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]
2016-12-28 自動配線用にdsn吐き出し
    [AXIS_SENSOR.sch, COM.sch, Charger.sch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]
2016-12-28 製造ファイル出力
    [KERISEv2-B.Cu.gbl, KERISEv2-B.Mask.gbs, KERISEv2-B.SilkS.gbo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]
2017-01-08 新基板用コード移植
    MicroMouse2016より
2017-01-08 PIDパラメータの調整
2017-01-08 MATLABファイルを追加
2017-01-09 壁センサがサチらないように調整
2017-01-09 壁センサの調整
2017-01-09 リフレクタの調整
2017-01-09 サインカーブの軌跡生成
    [data.csv]
2017-01-10 直線を含まないカーブの生成
    [data.csv]
2017-01-10 新しい軌跡追従の書き始め
2017-01-10 制御方法を変更
    カーブごとに独立制御
    カーブをつなぐ直線で速度を整える
2017-01-10 サインカーブの角加速度と最大角速度を固定
    [data.csv]
2017-01-11 角加速度を小さく
    [data.csv]
2017-01-11 安定走行
    [data.csv]
2017-01-12 ハーフで探索&最短
    帰りはまだ．
2017-01-12 速度一定の自律走行(クラシック)
    [data.csv]
2017-01-15 symsを使って軌道生成
    [data.csv]
2017-01-15 UIを改良
2017-01-17 ハーフで探索&最速
2017-01-17 45度軌道生成
    [data.csv]
2017-01-19 45度から60度に変更して壁を避ける
    [data.csv]
2017-01-19 ode45で軌道生成
    [data.csv]
2017-01-19 横壁補正
2017-01-20 150度カーブを2区画から3区画に変更
    8の字が不可能に．
2017-01-21 探索中の事故に備えて再開可能に
    [data.csv]
2017-01-21 直線の加速を3次曲線に．
    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
    [data.csv]
2017-01-22 探索中，次の行き先が決まるまで止まるように変更
    [data.csv]
2017-01-24 起動時にクラッシュするバグを修正
    リフレクタのキャリブレーションに失敗していた
2020-05-02 add gitignore
    [KERISEv2-B.Cu.gbl, KERISEv2-B.Mask.gbs, KERISEv2-B.SilkS.gbo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]
